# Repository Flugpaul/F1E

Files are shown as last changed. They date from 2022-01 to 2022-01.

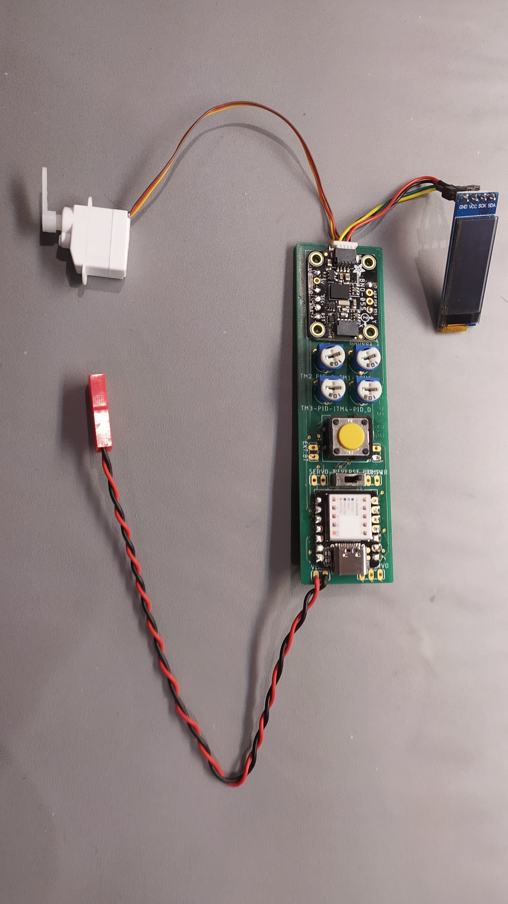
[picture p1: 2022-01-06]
Bild1.jpg

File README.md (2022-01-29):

# F1E
After the German championship 2021 in the aeromodelling category F1E with successful flights with new lightweight wings (build by Vchyaeslav Bolgov https://www.facebook.com/vabolgov ) I decided to renew my model strategy for F1E based on this experience. 
One main part of my thought was: which steering device I should use? All of my and Daniela’s models use multiple versions of steering and in also different professional conditions. My view about the fence to successful pilots let me understand, that for the design of my models a renew of the wing load should be one of the priorities. 
After some research I decided to build up my own steering.  The specifications were: 

•	The magnetic field and the heading should be detected with an electronic sensor.

•	The evaluation of the course deviation should be processed by a microprocessor (Arduino)

•	The whole steering device should be exchangeable with the traditional magnet	steering

•	The steering should work standalone without the direct dependency from an electronical timer

•	The steering should be prepared for an interface to an electronical timer

•	The usage of the steering should be reduced only to one function, which define the flight direction and the trimming for flying straight ahead.

• The design should have the potential to be developed to an lightweight steering unit.

Due to my status of early retirement in May 2021, end of the main paragliding season in 2021, and the Corona restrictions I used the late autumn and beginning winter time 2021/2022 for the own electronical design. Now the first prototype is ready, and I am very satisfied about the result. 

One of the most challenging issues was the choice of an appropriate magnetic sensor. I had a lot of unsuccessful attempts, but at least I found a very good alternate, which could calculate the needed heading without interferences from pitch and roll movements. 

The research was very time-consuming, so I decided to make all details like the coding and the circuit diagram pubic via the github repository (https://github.com/Flugpaul/F1E ). As a former manager for knowledge management in a worldwide company I know that sharing knowledge is useful for the progress of development.  With starting the first flight evaluations I will complete the content. 

A short indroduction for the use of this steering you will find here: https://vimeo.com/663940238 

Feel free to use, comment, add, discuss what I have designed. I would be happy about the feedback from the freeflight/F1E community. 😊 

Thx for the support and motivation to Johannes Seren ("make it more professional from the beginning") and Thomas Seren ("include a PID-controller for a good damping")

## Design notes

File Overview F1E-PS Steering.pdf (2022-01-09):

## F1E-Steering - Overview connectors F1E-PS device (© Paul Seren 2022)

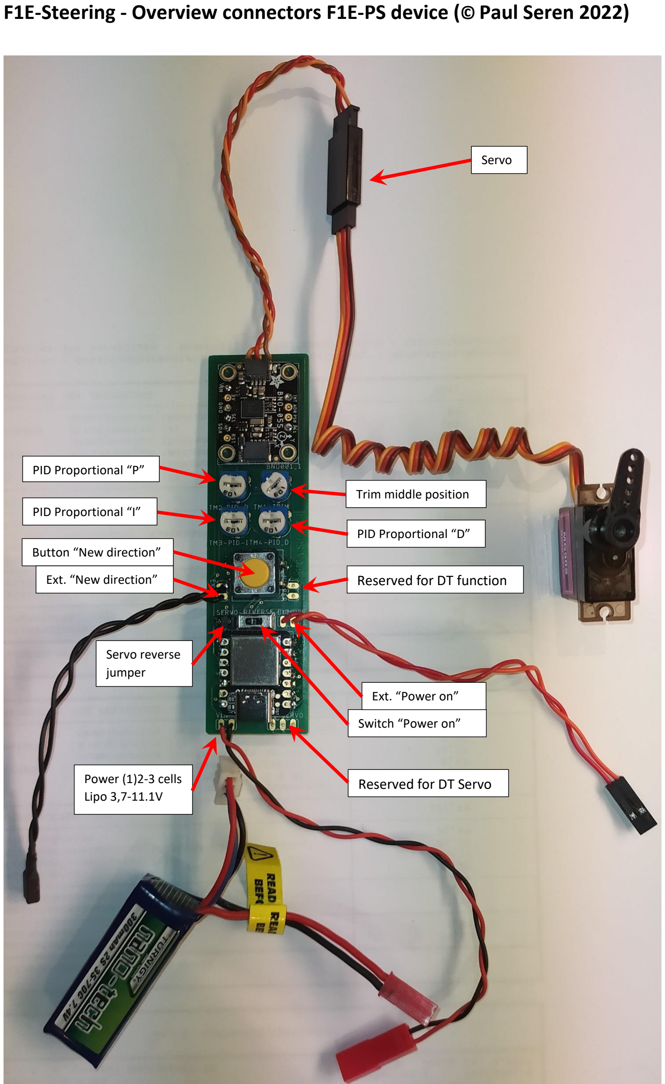
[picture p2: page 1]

Copyright: Paul Seren 2022

PID Proportional “P”

Power (1)2-3 cells
Lipo 3,7-11.1V

Switch “Power on”

Servo

Button “New direction”

Ext. “New direction”

Trim middle position
PID Proportional “I”
PID Proportional “D”

Ext. “Power on”

Servo reverse
jumper

Reserved for DT function

Reserved for DT Servo

## Servo

Connection to the servo

## Trim middle position

By pressing the Button “New direction” / Ext. “New direction” and adjust the Trim potentiometer at the same time you can adjust the middle position of the servo/(rudder)

## PID Proportional “P”

By adjusting the PID Proportional “P” you can adjust the angle amplitude of the ruder for the deviation from the desired direction to the individual characteristics of your model

## PID Proportional “I”

By adjusting the PID Proportional “I” you can adjust the | ruder for the deviation from the desired direction to the
individual characteristics of your model

## PID Proportional “D”

By adjusting the PID Proportional “D” you can adjust the | ruder for the deviation from the desired direction to
the individual characteristics of your model.

## Reserved for DT function

Usable for further development of the device for the communication with a timer or RDT. Not enabled in version V 0.9

## Reserved for DT Servo

Usable for further development of the device for the communication with a timer or RDT. Not enabled in version V 0.9

## Switch “Power on” / Ext. “Power on”

+ Power Switch onboard or via external wiring

## Button “New direction” / Ext. “New direction”

Most important button: Pressing the button (or using a button with the external wiring) will define the new direction and set the Servo to the defined/trimmed middle position. Each pressing of the button will use the current heading as the new direction.

## Servo reverse jumper

The default is set for a head-steering as a conventional steering with a physical magnet in front of the F1E-model. If you want to use the steering with a vertical tail at the tailplane, you can change the servo / deviation correction direction with a jumper bridge (2,54 mm)

## Power (1)2-3 cells / Lipo 3,7-11.1V

An on board internal constant voltage sensor provide a Vin Voltage from 3.7 – 11.1 V. Two cells Lipo (“2S / 7.4 V”) is recommended.

## How to use the device

- Connect the power (Lipo 2S/7.4 V recommended)
- Power Switch on
- Two green LED from the microcontroller and sensor will appear

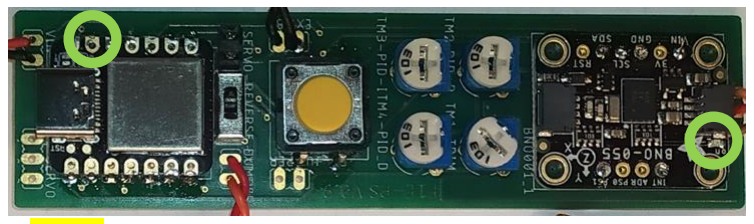
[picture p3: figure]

- A yellow LED will start blinking

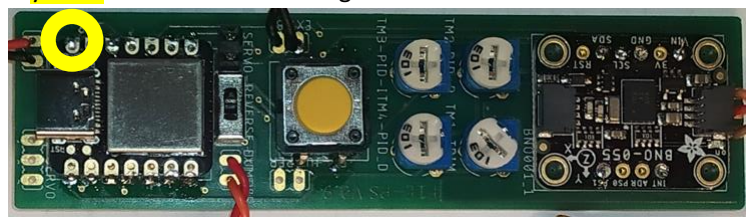
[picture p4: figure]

- The F1E-rudder-Servo will go to a position of maximum
- This yellow blinking and the Servo amplitude indicate that a calibration is necessary
- Calibration:
- 1. Take the device in your hand and “write” an imaginary “8”. This will calibrate the magnetic sensor!
- 2. Lay the device/the model nearly flat on the floor. Do not touch/move for a moment. This will calibrate the earth gravity. (The order of both calibration could be changed
- When the calibration is finished
- The yellow LED will glow permanenty
- The F1E-rudder-Servo will move to the adjusted middle position
- The device is now ready for the next flight
- Flying
- After successful calibration:
- Press the yellow “New direction” Button:
- The Servo will move the rudder to middle /neutral position
- Start you model
- Have fun and success!
- Trimming

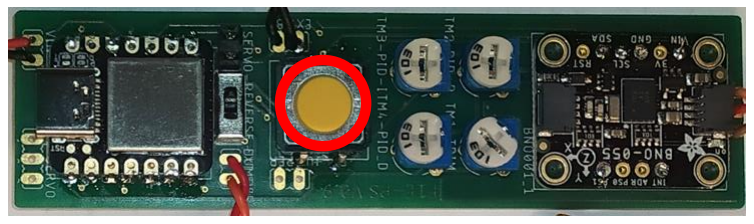
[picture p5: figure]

- After successful calibration:
- Press and hold the yellow “New direction” Button:
- The Servo will move the rudder to middle /neutral position
- Adjust with the Trim potentiometer the Servo

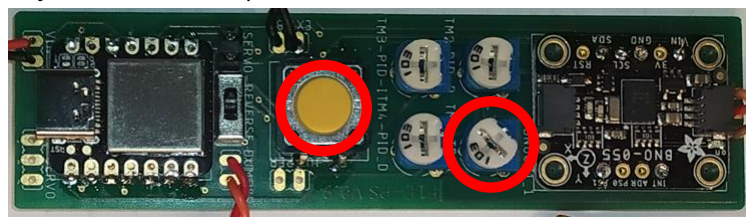
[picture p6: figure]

- Trimming the amplitude of the rudder
- After successful calibration:
- Adjust with the PID – P potentiometer the amplitude

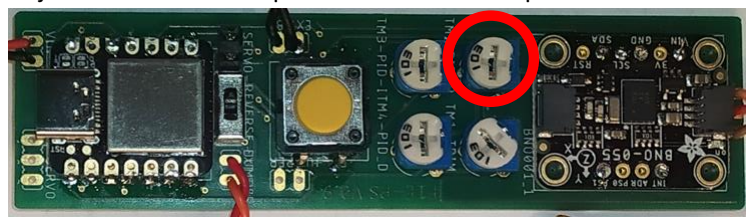
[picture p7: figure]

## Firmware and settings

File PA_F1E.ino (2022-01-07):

/**************************************************************************/
/*
 F1E-Steering with Sensor Adafruit BNO055 (Orientation-Fusion in sensor) 
 and Seeduino Xiao
 Moves the servo if there is a deviation to desired/wanted direction 
 tested with UNO and NANO Boards
 written for ARDUINO
 Paul Seren / Germany / 07.01.2022 Ver. 0.9
*/
/**************************************************************************/
#include <Wire.h>
#include <Adafruit_Sensor.h>
#include <Adafruit_BNO055.h>
#include <utility/imumaths.h>

// Lib. for OLED Display
#include <Adafruit_GFX.h>
#include <Adafruit_SSD1306.h>
#define SCREEN_WIDTH 128 // OLED display width, in pixels
#define SCREEN_HEIGHT 32 // OLED display height, in pixels
// Declaration for an SSD1306 display connected to I2C (SDA, SCL pins)
#define OLED_RESET     -1 // Reset pin # (or -1 if sharing Arduino reset pin)
Adafruit_SSD1306 display(SCREEN_WIDTH, SCREEN_HEIGHT, &Wire, OLED_RESET);

#include <Servo.h> // use of the PWM-library
//#include <Adafruit_TiCoServo.h> 

// Set the delay between fresh samples /
#define BNO055_SAMPLERATE_DELAY_MS (100)
// Check I2C device address from BNO055 and correct line below (by default address is 0x29 or 0x28)
//                                   id, address
Adafruit_BNO055 bno = Adafruit_BNO055(55, 0x28);

// Variables for sensor evaluation
float roll, pitch, heading;
int delayTime=500;

char * RevText = "F1E-Control - Rev.0.9";
// Variables for some conversion stuff

// Variables for direction change / F1E_Servo_Move ()

int current_Bearing = 180;                          // INT-Variable for current heading
int wanted_Bearing = 180;                           // INT-Variable for desired heading
int delta_Bearing;                                  // INT-(+-)Variable for deviation from desired heading

// Servo Variables

int servoPinF1E     =  9;    // Servo Pin for <Adafruit_TiCoServo.h> library to avoid servo jitters https://forums.adafruit.com/viewtopic.php?f=22&t=96847 
                          // https://learn.adafruit.com/neopixels-and-servos/the-ticoservo-library
int minGrad      =  45;   // minimum servo position  45°
int maxGrad     =  135;   // maximum servo position  135°
int centerGrad  = 90;     // midle position Servos
int servoPinDT    =   10;   // Dummy Servo for later use
int servoDirection = 1;   // Servo sign (+/-)

int servoPos;             // Servo position
int servoPosDT;             // Servo position for later use


// Servo-Trimmungs-Varianten
const int potiPin = A0;   // Analog-Input for Trimpoti
int sensor = 0;           // sensor-Value on Analog-Input (0 - 1023) 
int pwm_F1E = 0;              // calculated sensor-value for the PWM-Trim-Value (-maxTrim/2 bis + maxTrim/2)
int pwmOld = 0;           // PWM-value to remember for next loop
int maxTrim = 40;         // max. Trim-degrees

//Servo für ToCoServo.h   servoF1E; 
//Adafruit_TiCoServo servoF1E; 
// Adafruit_TiCoServo servoDT; 
//Servo für servo.h 
Servo servoF1E; 
Servo servoDT; 
// Button Variables
int SW1          =  6;    // Input button / digital pin:  input for desired heading and trimming 
int SW2          =  8;    // Input button / digital pin:  input for DT-Timer-Function for later use 
int SW3          =  7;     // Input button / digital pin: sign (+/-) for Servo direction. 

//PID-correction

int abs_delta_Bearing = 0; 
int abs_delta_Bearing_n1 = 0; // default value deviation one measurement before
int abs_delta_Bearing_n2 = 0; // default value deviation two measurements before
int PID_Input;
int PID_Output;

float sensor_P;
float sensor_I;
float sensor_D;

float PID_Kp = 1.0;
float PID_Ki = 0;
float PID_Kd = 0;

int PID_potiPin = A1; 

 
void setup() {

// Initialize OLED Display
  display.begin(SSD1306_SWITCHCAPVCC, 0x3C);
  display.clearDisplay();
  display.display();
  display.clearDisplay();
  display.setTextColor(WHITE);
  display.setCursor(1,1);
  display.setTextSize(1);
  display.println(RevText);
  display.display();
  delay(1000);
  
  
 /* Initialise serial Com Board*/
 // SerialUSB.begin(9600);
 //Serial.begin(115200);
  //while (!Serial) yield();

  /* Initialise the internal LED for calibration Status servo */
  pinMode(LED_BUILTIN,OUTPUT);

  // Set the switch-Buttons
  pinMode(SW1,INPUT);           // define button type
  digitalWrite(SW1,HIGH);       // button default High
  pinMode(SW2,INPUT);           // define button type
  digitalWrite(SW2,HIGH);       // button default High
   pinMode(SW3,INPUT);           // define button type
  digitalWrite(SW3,HIGH);       // button default High
  
  /* Initialise the servo */
  servoF1E.attach(servoPinF1E);    // connect Servo F1E
  servoDT.attach(servoPinDT);    // connect Servo DT
  servoPos = centerGrad;        // move servo to default midle position

  /* Initialise the sensor */
  if(!bno.begin())
  {
    /* There was a problem detecting the BNO055 ... check your connections */
    // SerialUSB.print("Ooops, no BNO055 detected ... Check your wiring or I2C ADDR!");
      /* display.clearDisplay();
       display.println("No BNO055 detected");
       display.display();
        */
     Oprintln ("No BNO055 detected");
     while(1);
  }

    Oprintln ("BNO055 detected");
    delay (1000);
  /* 
  displaySensorDetails();
  displaySensorStatus();
  displayCalStatus();
  */
  servoF1E.write(minGrad);
 
  // Check calibration status in a loop. End setup only, when calibration is sufficient
  //Calibrate
  Oprintln ("Calibration started");
  while (Analyse_CalStatus())
  {
  //Serial.println("Not yet sufficiant calibrated");
  digitalWrite(LED_BUILTIN, HIGH);
  delay(delayTime);
  digitalWrite(LED_BUILTIN, LOW);
  delay(delayTime);
  }
  
  digitalWrite(LED_BUILTIN, HIGH);
  delay(2000);
  digitalWrite(LED_BUILTIN, LOW);
  Oprintln ("Calibration ended!");
  delay(1000);
  F1E_Get_PID_K ();
  
  if(!digitalRead(SW3))   
  {
  servoDirection = (-1*servoDirection);
  Oprintln ("Servo reverse" );
  delay (1000);
  } 
  
  Oprintln ("Fly a Max! ");
  delay (1000);
  
  F1E_Get_Current_Bearing ();
  wanted_Bearing = current_Bearing; 
  
  F1E_Get_Wanted_Trim ();
  pwmOld = pwm_F1E; 
  F1E_Servo_Move ();
  
}



void loop() {
  
  F1E_Get_Current_Bearing (); 
  F1E_Get_Wanted_Bearing (); 
  F1E_Servo_Move ();
  //DT_Interupt ();
}

int Oprintln(char * PrintText)
{
  display.clearDisplay();
  display.setCursor(5,10);
  display.println(PrintText);
  display.display(); 
}

/**************************************************************************/
/*
    Analyse the Calibration status 
*/
/**************************************************************************/
bool Analyse_CalStatus ()
  {
  /* Get the four calibration values (0..3) */
  /* Any sensor data reporting 0 should be ignored, */
  /* 3 means 'fully calibrated" */
  uint8_t system, gyro, accel, mag;
  system = gyro = accel = mag = 0;
  bno.getCalibration(&system, &gyro, &accel, &mag);

  // If the sensor is not sufficient calibrated, return 1. 
  if (gyro > 2 && mag > 2)  {return 0;}
  return 1;    
  }

/**************************************************************************/
/*
    Determine the desired bearing 
*/
/**************************************************************************/
void F1E_Get_PID_K ()
  {
 
    PID_potiPin = A1;
    sensor_P = analogRead(PID_potiPin);
    PID_Kp = sensor_P/1023;
    
    PID_potiPin = A2;
    sensor_I = analogRead(PID_potiPin);
    PID_Ki = sensor_I/10230;

    PID_potiPin = A3;
    sensor_D = analogRead(PID_potiPin);
    PID_Kd = sensor_D/(2*1023);
  /* display.clearDisplay();
  display.setCursor(5,10);
  display.print(PID_Kp);
  display.print(" | ");
  display.print(PID_Ki);
  display.print(" | ");
  display.print(PID_Kd);
  display.display(); 
  */
    //Serial.print("sensor_P = ");
    //Serial.print(sensor_P);
    //Serial.print("PID_Kp = ");
    //Serial.print(PID_Kp);
    //Serial.print("|| sensor_I = ");
    //Serial.print(sensor_I);
    //Serial.print("PID_Ki = ");
    //Serial.print(PID_Ki);
    //Serial.print("|| sensor_D = ");
    //Serial.print(sensor_D);
    //Serial.print("PID_Kd = ");
    //Serial.println(PID_Kd);
    
  }  

/**************************************************************************/
/*
    Move DT Servo / do an action (Dummy for later use) 
*/
/**************************************************************************/
void DT_Interupt ()
{
if(!digitalRead(SW2))   
  {
  DT_Servo_Move ();
  }
}

/**************************************************************************/
/*
    Determine the desired trim 
*/
/**************************************************************************/
void F1E_Get_Wanted_Trim ()
  {
    // Check if there is a change necessary for the middle position 
    sensor = analogRead(potiPin);
    pwm_F1E = map(sensor, 0, 1023, 0, maxTrim) - maxTrim/2;
    
    // new wanted trim
    centerGrad = centerGrad - (pwm_F1E-pwmOld);
    // adjust min and max Grad
    minGrad=minGrad-(pwm_F1E-pwmOld);
    maxGrad=maxGrad-(pwm_F1E-pwmOld);
    pwmOld = pwm_F1E; 

    return;
  }
/**************************************************************************/
/*
    Determine the desired bearing 
*/
/**************************************************************************/
void F1E_Get_Wanted_Bearing ()
  {
  if(!digitalRead(SW1)) 
    { 
    // Check if there is a change necessary for the middle position 
    F1E_Get_Wanted_Trim ();
    
    // new wanted bearing
    wanted_Bearing = current_Bearing;
    
   
    // Move servo position to the (new) middle position
    // servoPos = centerGrad;
    //Serial.print("Sensor = ");
    //Serial.print(sensor);
    //Serial.print("Centergrad = ");
    //Serial.print(centerGrad);
    //Serial.print(" pwm_F1E  = ");
    //Serial.println(pwm_F1E);
  
    //Serial.print("Direction button pressed - new direction and trim"); 
    //Serial.println();
    F1E_Get_PID_K ();
       
    }  
   return;
  }

/**************************************************************************/
/*
    Moves the serco if there is a deviation to desired/wanted direction 
*/
/**************************************************************************/
void F1E_PID ()
  {
  
  PID_Input = abs_delta_Bearing ; 
  // Output mit PID - Kp modifizieren 
  F1E_Get_PID_K ();
  PID_Output = PID_Kp * abs_delta_Bearing + PID_Ki * (abs_delta_Bearing + abs_delta_Bearing_n1 + abs_delta_Bearing_n2) + PID_Kd * (abs_delta_Bearing - abs_delta_Bearing_n1); 
  }
/**************************************************************************/
/*
    Moves the F1E-servo if there is a deviation to desired/wanted direction 
*/
/**************************************************************************/
void F1E_Servo_Move ()
  {
    delta_Bearing =  wanted_Bearing - current_Bearing; 
    //Modulo for beeing aware to 0/360° change of direction and calculation only the deviation/direction for corretion  
    //Serial.print("Modulo degrees change from desired direction: "); 

    //Remember to previous delta_bearing - they will be used for PID calculation
    abs_delta_Bearing_n2 = abs_delta_Bearing_n1;
    abs_delta_Bearing_n1 = abs_delta_Bearing;
    abs_delta_Bearing = ((delta_Bearing + 540) % 360) - 180; 

     
    F1E_PID();
    //servoPos = centerGrad - PID_Output;
    servoPos = centerGrad - (servoDirection*PID_Output);
    
     display.clearDisplay();
     display.setCursor(5,18);
     display.println(servoPos);
     display.setCursor(30,18);
     display.println(wanted_Bearing);
     display.setCursor(50,18  );
     display.println(current_Bearing);
     display.display(); 
     //delay (10);
    // Limitation of correction  
    if(servoPos > maxGrad) {servoPos = maxGrad;} 
    if(servoPos < minGrad) {servoPos = minGrad;} 
    
    // go to new Servo position
    servoF1E.write(servoPos);
    
   return;
  }
/**************************************************************************/
/*
    Moves the DT-servo if there is a deviation to desired/wanted direction 
*/
/**************************************************************************/
void DT_Servo_Move ()
  {
/*Aktuell noch Dummy Code um überhaupt was zu tun*/

       
    // go to new Servo position
    servoPosDT = 90;
    servoDT.write(servoPosDT);
    delay (1000);
    servoPosDT = 135;
    servoDT.write(servoPosDT);
    delay (1000);
    servoPosDT = 45;
    servoDT.write(servoPosDT);
    delay (1000);
  }


/**************************************************************************/
/*
    Displays some basic information on this sensor from the unified
    sensor API sensor_t type (see Adafruit_Sensor for more information)
*/
/**************************************************************************/
void displaySensorDetails(void)
{
  sensor_t sensor;
  bno.getSensor(&sensor);
  //Serial.println("------------------------------------");
  //Serial.print  ("Sensor:       "); //Serial.println(sensor.name);
  //Serial.print  ("Driver Ver:   "); //Serial.println(sensor.version);
  //Serial.print  ("Unique ID:    "); //Serial.println(sensor.sensor_id);
  //Serial.print  ("Max Value:    "); //Serial.print(sensor.max_value); //Serial.println(" xxx");
  //Serial.print  ("Min Value:    "); //Serial.print(sensor.min_value); //Serial.println(" xxx");
  //Serial.print  ("Resolution:   "); //Serial.print(sensor.resolution); //Serial.println(" xxx");
  //Serial.println("------------------------------------");
  //Serial.println("");
  delay(500);
}

/**************************************************************************/
/*
    Display some basic info about the sensor status
*/
/**************************************************************************/
void displaySensorStatus(void)
{
  /* Get the system status values (mostly for debugging purposes) */
  uint8_t system_status, self_test_results, system_error;
  system_status = self_test_results = system_error = 0;
  bno.getSystemStatus(&system_status, &self_test_results, &system_error);

  /* Display the results in the Serial Monitor */
  //Serial.println("");
  //Serial.print("System Status: 0x");
  //Serial.println(system_status, HEX);
  //Serial.print("Self Test:     0x");
  //Serial.println(self_test_results, HEX);
  //Serial.print("System Error:  0x");
  //Serial.println(system_error, HEX);
  //Serial.println("");
  delay(500);
}

/**************************************************************************/
/*
    Display sensor calibration status
*/
/**************************************************************************/
void displayCalStatus(void)
{
  /* Get the four calibration values (0..3) */
  /* Any sensor data reporting 0 should be ignored, */
  /* 3 means 'fully calibrated" */
  uint8_t system, gyro, accel, mag;
  system = gyro = accel = mag = 0;
  bno.getCalibration(&system, &gyro, &accel, &mag);

  /* The data should be ignored until the system calibration is > 0 */
  //Serial.print("\t");
  if (!system)
  {
    //Serial.print("! ");
  }

  /* Display the individual values */
  //Serial.print("Sys:");
  //Serial.print(system, DEC);
  //Serial.print(" G:");
  //Serial.print(gyro, DEC);
  //Serial.print(" A:");
  //Serial.print(accel, DEC);
  //Serial.print(" M:");
  //Serial.print(mag, DEC);
}

/**************************************************************************/
/*
    determine current heading
*/
/**************************************************************************/
void F1E_Get_Current_Bearing ()
 {
 imu::Vector<3> euler = bno.getVector(Adafruit_BNO055::VECTOR_EULER);
 heading = euler.x();
 current_Bearing = heading; // Wandlung auf int

  /* Display the floating point data */
  //Serial.print("X: ");
  //Serial.print(euler.x());
  //Serial.print(" Y: ");
  //Serial.print(euler.y());
  //Serial.print(" Z: ");
  //Serial.print(euler.z());
  //Serial.print("\t\t");
  
// print the heading, pitch and roll    Serial.print("Orientation: ");
  //Serial.print(heading);
  //Serial.print(", ");
   //Serial.print(current_Bearing);
  //Serial.print(", ");
  //Serial.print(wanted_Bearing);
  //Serial.print(", ");
  //Serial.print(pitch);
  //Serial.print(", ");
  //Serial.println(roll);
}
